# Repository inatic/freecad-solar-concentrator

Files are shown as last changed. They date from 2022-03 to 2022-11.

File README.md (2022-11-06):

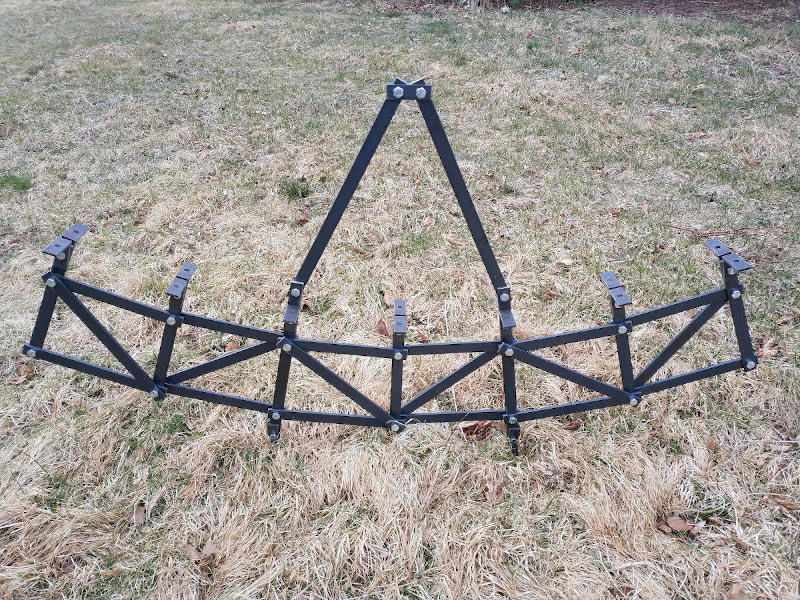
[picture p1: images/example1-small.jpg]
Example1


The script in this repository creates a support structure for a parabolic mirror. Code is written in Python and runs in [FreeCAD](freecad), which is an open-source CAD/CAM package. It can be cloned from [Github][github] and needs to be placed in the `Macro` directory of your FreeCAD installation. To find where that is, start FreeCAD and click **Edit | Preferences | General | Macro** to have a look at the `Macro path` setting. The following uses the default location on my [Ubuntu][ubuntu] installation.

```
cd ~/.local/share/FreeCAD/Macro
git clone https://github.com/inatic/freecad-solar-concentrator solar
```

The script is executed in FreeCAD by simply importing it from the *Python Console*, which can be activated under *View | Panels | Python Console*. When all goes well this creates a document containing a parabola shaped truss as well as a cutlist for the bars that are used to build it. Parameters in the script allow changing the shape and size of the parabola as well as the design of the truss. Once imported and after making modifications to the script, reloading is done using the `importlib.reload()` method.

```
from solar import concentrator
import importlib
importlib.reload(concentrator) 
```

# SCRIPT

The following explains how the script works and should allow for easy customization. It also includes some general information on scripting in FreeCAD. As any typical script it starts by importing the necessary modules, and then checks for an open FreeCAD document, which if absent is created.

```python
import Part, Draft, math, copy
import FreeCAD
from FreeCAD import Base

doc = FreeCAD.ActiveDocument
if not doc:
    doc = FreeCAD.newDocument()
```

## PARABOLA

A parabola is defined by a point named the `focus`, which is where the light will be concentrated, and an axis named the `directrix` which in our case comes under and along the length of the parabola. For each point on the parabola, its perpendicular distance to the directrix should equal its distance to the focus. Instead of a directrix our script defines a `center` or `vertex` to the same effect, this is a point on the parabola's axis of symmetry that is midway between `focus` and `directrix`. A parabola is a mathematical construct that is not limited in size, any point that has equal distances to focus and directrix is part of the parabola. The reflective surface of a concentrator however has `endpoints` and these are specified as its `parameters`. 

Parabola

The `Part` module is then used to create such a parabola in FreeCAD. The `Center` of this particular parabola is chosen at the coordinate system origin, the plane of the parabola is chosen to be perpendicular to the y-axis (`Axis`), and the parabola is oriented along the positive Z-Axis (`XAxis`). The distance between the `Center` of the parabola and its focus is referred to as its `Focal` distance. Endpoints to both sides of the parabola are specified as distances along its `directrix` (which in this case is parallel to the x-axis), starting from the origin and going in both directions (`parameter1` and `parameter2`). Turning the mathematical curve into an `edge` shape that can be added to the document is done using the `toShape` method, taking previous parameters as arguments.

Parabola

```python
focalDistance = 1000
parameter1 = -1500
parameter2 = 1500

parabola = Part.Parabola()
parabola.Center = FreeCAD.Vector(0,0,0)
parabola.Axis = FreeCAD.Vector(0,1,0)
parabola.XAxis = FreeCAD.Vector(0,0,1)
parabola.Focal = focalDistance
edge = parabola.toShape(parameter1, parameter2)
objectParabola = doc.addObject('Part::Feature', 'Parabola')
objectParabola.Shape = edge
objectFocus = doc.addObject('Part::Feature', 'Focus')
pipe = Part.Face(Part.Wire(Part.makeCircle(50, parabola.Focus, parabola.Axis))).extrude(parabola.Axis*20)
objectFocus.Shape = pipe
```

## TRUSS

For the mirror to follow the curve of a parabola, it needs to be supported by a rigid and sufficiently accurate structure. The idea is to create a number of parabola-shaped ribs on which mirrors are mounted. Each rib is constructed as a truss which makes it relatively strong and easy to fabricate. The mirror mounts to a piece of bar stock (e.g. 20x5mm hot rolled steel), and the bar stock mounts to angle brackets that are spaced along the length of the parabola (`bracketSpacing`). Spacing is calcuated by dividing the parabola in a number of equal length `subdivisions`. For each bracket the parameter on the parabola (coordinate on the directrix) is calculated, followed by the vector of its location, and the vector normal to the parabola at that location (see illustration). The normal vector determines the direction of truss members that point down from the back of the parabola. As these truss members are oriented normal (perpendicular) to the parabola I'm going to refer to them as *normal* members. Each `normal` member has 5 holes: holes at top and bottom to mount other components, a hole for mounting the bracket, one for mounting upper chords, and one for mounting lower chords. At the top mounting holes a structure will be attached to hold something like a tube carrying water at the focus, and the bottom mounting holes attach to a beam that holds all the ribs and turns with the sun. The location of these holes is measured as an offset from the reflective surface of the parabola and respectively named `topMountOffset`, `bracketOffset`, `upperChordOffset`, `lowerChordOffset` and `bottomMountOffset`. Each *normal* member in the `normalMembers` list stores hole location vectors. As these are hole locations, bars themselves need to be longer and each truss member is extended by a distance referred to as `lengthExtension`.

Truss

```python
subdivisions = 9
topMountOffset = 25
bracketOffset = 25
upperChordOffset = bracketOffset + 50
lowerChordOffset = bracketOffset + 250
bottomMountOffset = 50

bracketSpacing = edge.Length/subdivisions

normalMembers = []
for i in range(0, subdivisions + 1):
    bracketPosition = i*bracketSpacing
    parameter = edge.getParameterByLength(bracketPosition)
    normal = edge.normalAt(parameter).normalize()
    pointOnParabola = edge.valueAt(parameter)
    topMountPoint = pointOnParabola + topMountOffset*normal
    bracketMountPoint = pointOnParabola - bracketOffset*normal
    upperChordMountPoint = pointOnParabola - upperChordOffset*normal
    lowerChordMountPoint = pointOnParabola - lowerChordOffset*normal
    bottomMountPoint = lowerChordMountPoint - bottomMountOffset*normal
    normalMembers.append( (topMountPoint, bracketMountPoint, upperChordMountPoint, lowerChordMountPoint, bottomMountPoint) )
```

Other members of the truss are quite easy to create - they just connect the holes of adjoining normal truss members. Upper and lower chord members of the truss are created in this way, as are the diagonal members that form triangles and are drawn in a zig-zag pattern.

```python
upperChords = []
for i in range(0,len(normalMembers)-1):
    upperChordPoint0 = normalMembers[i][2]
    upperChordPoint1 = normalMembers[i+1][2]
    upperChords.append((upperChordPoint0, upperChordPoint1))

lowerChords = []
for i in range(0,len(normalMembers)-1):
    lowerChordPoint0 = normalMembers[i][3]
    lowerChordPoint1 = normalMembers[i+1][3]
    lowerChords.append((lowerChordPoint0, lowerChordPoint1))

diagonals = []
for i in range(0,len(normalMembers)-1):
  if (i % 2) == 0:
    diagonalPoint0 = normalMembers[i][2]
    diagonalPoint1 = normalMembers[i+1][3]
  else:
    diagonalPoint0 = normalMembers[i][3]
    diagonalPoint1 = normalMembers[i+1][2]
  diagonals.append((diagonalPoint0,diagonalPoint1))
```

## COLLECTOR

Solar energy is concentrated and the resulting heat collected at the focal point of the parabola, where a collector is held in place by a supporting truss structure. As the collector builds on this structure, some distance (`supportOffset`) is left between the end of the support structure and the focal point of the parabola. The top of the support structure (`supportTopWidth`) is narrower than its bottom, and a number of web members (`webMembers`) give the structure additional strength. At the bottom the support structure attached to the normal members of the parabola's truss. If there is an even number of normal members, the structure attaches to the pair in the middle. If there is an odd number of normal members, the pair adjacent to the middle normal member is used to connect the collector structure. Attachment points are named `supportBase1` and `supportBase2`.

```python
collectorOffset = 150
supportTopWidth = 30
webMembers = 5

collectorSupportMembers = []

num = len(normalMembers)
if num % 2 == 0:
  # even number of members
  indexMember1 = int(num/2 - 1)
  indexMember2 = int(num/2)
else:
  # odd number of members
  indexMember1 = int((num+1)/2 - 2)
  indexMember2 = int((num+1)/2)

supportBase1 = normalMembers[indexMember1][0]
supportBase2 = normalMembers[indexMember2][0]
```

Endpoints for side members are determined by starting at the focus of the parabola, subtracting `collectorOffset`, and moving half of `supportTopWidth` to each side. Members are then added to the `collectorSupportMembers` list.

```python
uDirection = (parabola.Focus - parabola.Center).normalize()
vDirection = (supportBase1 - supportBase2).normalize()
supportTop1 = parabola.Focus - collectorOffset*uDirection + (supportTopWidth/2)*vDirection
supportTop2 = parabola.Focus - collectorOffset*uDirection - (supportTopWidth/2)*vDirection

collectorSupportMembers.append([supportBase1, supportTop1])
collectorSupportMembers.append([supportBase2, supportTop2])
collectorSupportMembers.append([supportTop1, supportTop2])
```

A number of web members (`webMembers`) connect at regular intervals along the length of the side members in a zigzag pattern. Points on side members are specified in terms of their respective direction vectors `dir1` and `dir2`. 

```python
dir1 = (supportTop1 - supportBase1).normalize()
dir2 = (supportTop2 - supportBase2).normalize()
sideMemberLength = (supportTop1 - supportBase1).Length
webMemberStep = sideMemberLength / webMembers

for i in range(1, webMembers):
  if i % 2 == 0:
    height1 = (i-1) * webMemberStep
    height2 = i * webMemberStep
  else:
    height2 = (i-1) * webMemberStep
    height1 = i * webMemberStep
  point1 = supportBase1 + height1*dir1
  point2 = supportBase2 + height2*dir2
  collectorSupportMembers.append([point1, point2])
```

## BARS

Each bar is represented by a `Bar` object, which is drawn over the lines of the truss and attaches to other bars at the intersection points of the truss (`holes`). The hole coordinates for different types of bars are stored in lists `normalMembers`, `upperChords`, `lowerChords` and `diagonals`. Each `Bar` object has its own coordinate system (u,v,w) that helps creating the necessary geometry. The axis perpendicular to the parabola corresponds to the `w` axis of the bar, while the `u` axis points along the length of the bar. Bars are offset along the wAxis (`wAxisOffset`) so they don't overlap. A `lengthExtension` parameter extends the bar to both sides, starting at the outer holes. A `Bar` object furthermore has a `width`, `thinkness` and a diameter for its holes (`holeDiameter`). It also has a `name` that identifies the bar in the FreeCAD document and should probably be written on the physical bar to keep track of its location in the truss. 

Bar

```python
class Bar:
    def __init__(self, holes, wAxis, wAxisOffset, lengthExtension, width, thickness, holeDiameter, name):
        self.holes = holes
        self.wAxis = wAxis
        self.wAxisOffset = wAxisOffset
        self.lengthExtension = lengthExtension
        self.width = width
        self.thickness = thickness
        self.holeDiameter = holeDiameter
        self.name = name
        self.offsetHoles = [hole + self.wAxisOffset*self.wAxis for hole in self.holes]
        # Local coordinate system
        firstHole = self.offsetHoles[0]
        lastHole = self.offsetHoles[-1]
        self.u = (lastHole - firstHole).normalize()
        self.w = self.wAxis
        self.v = self.w.cross(self.u)
```

The `getShape` method of a `Bar` object creates a `Part` shape that can be added to the FreeCAD document. It starts with the offset hole positions and uses the `Bar` object's coordinate system (`uvw`) to create corner points and connects them to create a face. Holes are cut out of this face and the result is extruded to create a solid bar.

```python
def getShape(self):
    firstHole = self.offsetHoles[0]
    lastHole = self.offsetHoles[-1]
    # Points
    holeDistance = (lastHole - firstHole).Length
    v1 = firstHole + (self.width/2)*self.v - (self.lengthExtension)*self.u
    v2 = v1 + holeDistance*self.u + 2*(self.lengthExtension)*self.u
    v3 = v2 - self.width*self.v
    v4 = firstHole - (self.width/2)*self.v - (self.lengthExtension)*self.u
    # Face
    line1 = Part.Edge(Part.LineSegment(v1, v2))
    line2 = Part.Edge(Part.LineSegment(v2, v3))
    line3 = Part.Edge(Part.LineSegment(v3, v4))
    line4 = Part.Edge(Part.LineSegment(v4, v1))
    wire = Part.Wire([line1, line2, line3, line4])
    face = Part.Face(wire)
    # Cut holes
    for hole in self.offsetHoles:
        circle = Part.Face(Part.Wire(Part.makeCircle(self.holeDiameter/2, hole, self.w)))
        face = face.cut(circle)
    solid = face.extrude(self.thickness*self.w)
    return solid
```

The `getHolePositions` method in turn provides the locations of holes in the bar, measured from the beginning of the bar. 

```python
def getHolePositions(self):
    positions = []
    firstHole = self.offsetHoles[0]
    lastHole = self.offsetHoles[-1]
    barStart = firstHole - (self.lengthExtension)*self.u
    for hole in self.offsetHoles:
        distanceFromStart = (hole - barStart).Length
        positions.append(distanceFromStart)
    return positions
```

## CUTLIST

Lengths of bars and the locations for holes to be drilled are added to a `SpreadSheet` object named `Cutlist`. This is done by iterating over `Bar` objects and fetching the positions of holes using the `getHolePositions` method. We're also keeping track of the total length of bar stock (`totalBarLength`) that is used to build the truss in order to have an estimate of material requirements. 

```python
totalBarLength = 0
for bar in bars:
    sheet.set('A'+str(row), bar.name)
    length = bar.getLength()
    totalBarLength += length
    sheet.set('B'+str(row), str(round(length,2)))
    holePositions = bar.getHolePositions()
    for j in range(0, len(holePositions)):
        column = chr(67+j)
        sheet.set(str(column)+str(row), str(round(holePositions[j],2)))
    row+=1
``` 

[freecad]: (https://www.freecadweb.org/)
[github]: (https://github.com/inatic/solar-concentrator)
[ubuntu]: (https://ubuntu.com/)

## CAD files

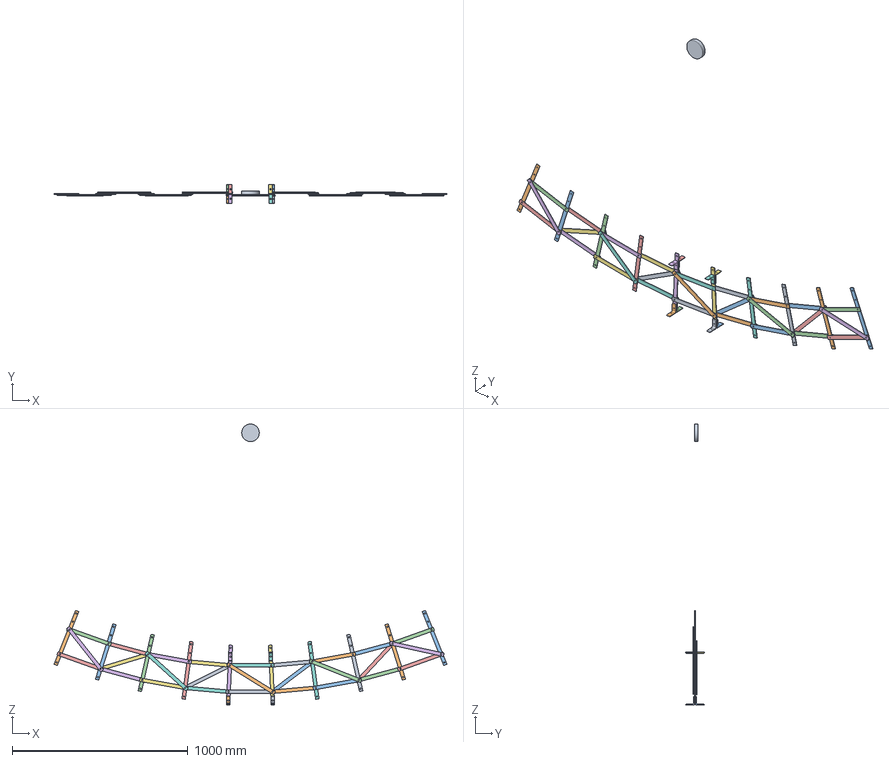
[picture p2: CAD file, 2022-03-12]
freecad/parabole-test-2.FCStd
2234.0 x 106.0 x 1597.2 mm
bracket-001
bracket-002
bracket-003
bracket-004
bracket-005
bracket-006
bracket-007
bracket-008
Focus
Normal1
Normal2
Normal3
Normal4
Normal5
Normal6
Normal7
Normal8
Normal9
Normal10
UpperChord1
UpperChord2
UpperChord3
UpperChord4
UpperChord5
UpperChord6
UpperChord7
UpperChord8
UpperChord9
LowerChord1
LowerChord2
LowerChord3
LowerChord4
LowerChord5
LowerChord6
LowerChord7
LowerChord8
LowerChord9
Diagonal1
Diagonal2
Diagonal3
Diagonal4
Diagonal5
Diagonal6
Diagonal7
Diagonal8
Diagonal9

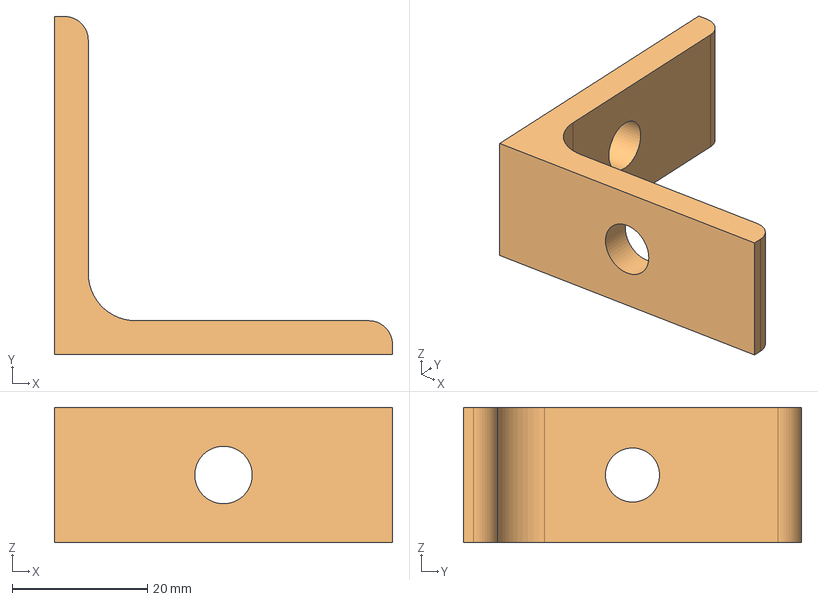
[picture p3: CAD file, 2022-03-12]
freecad/bracket.FCStd
50.0 x 50.0 x 20.0 mm
bracket

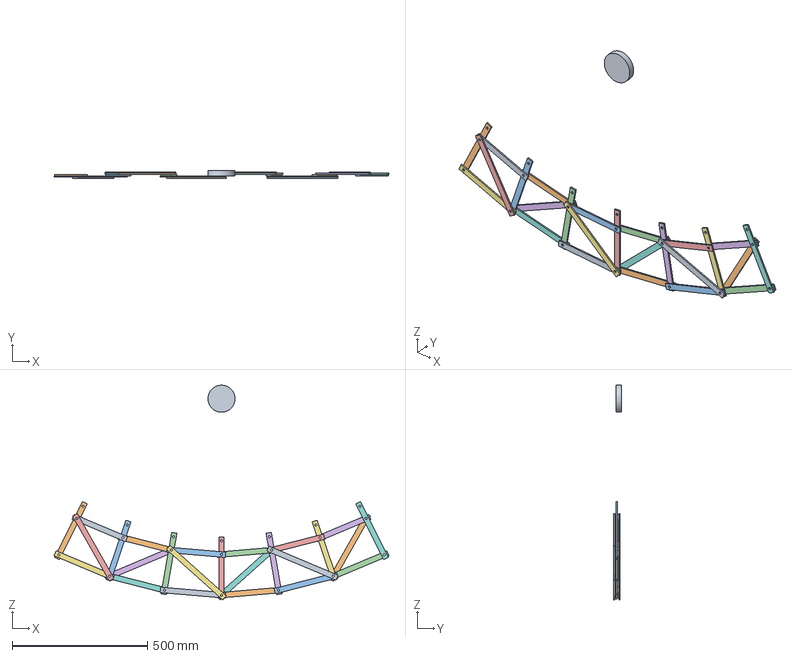
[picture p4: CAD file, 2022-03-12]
freecad/parabole-test-1.FCStd
1236.6 x 30.0 x 792.4 mm
Focus
Normal1
Normal2
Normal3
Normal4
Normal5
Normal6
Normal7
UpperChord1
UpperChord2
UpperChord3
UpperChord4
UpperChord5
UpperChord6
LowerChord1
LowerChord2
LowerChord3
LowerChord4
LowerChord5
LowerChord6
Diagonal1
Diagonal2
Diagonal3
Diagonal4
Diagonal5
Diagonal6
